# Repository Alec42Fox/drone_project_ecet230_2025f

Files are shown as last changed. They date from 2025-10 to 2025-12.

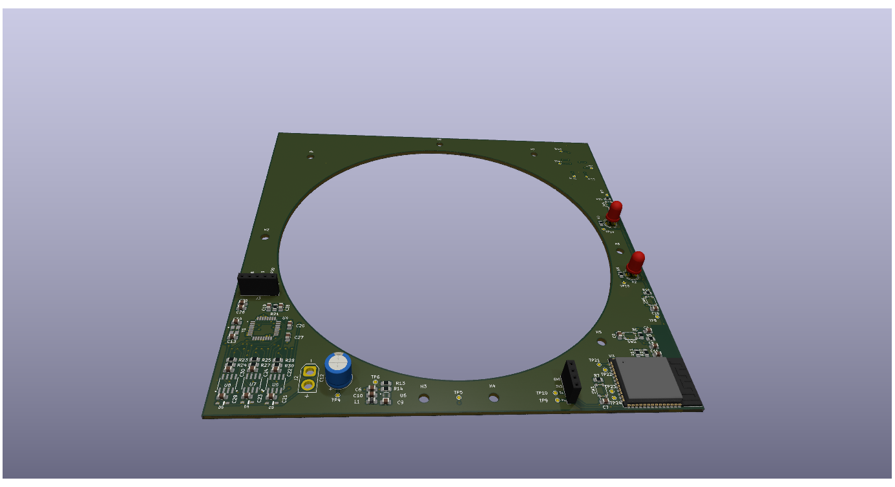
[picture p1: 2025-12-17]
Extra/HMS.png

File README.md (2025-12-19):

# ECET - 230 - 001 - HMS (Height Maintenance System)
* video of the prototype in action (fixed to a single axis)
* Also hyperlink to simulation below:
Watch the video (https://youtu.be/sBg5eHK91Yk)

View Our Project on CodePen (https://codepen.io/codaryu/pen/zxqgJxX)

## Goals
* Make a single propelled drone that hovers at a specific height and can get back to that height when outside forces act on it.
## Team Members
* Alec Fox - Programming
* Angelo McNeill - CAD Design
* Cristian D. Garcia S. - PCB Design
## Tools and Technologies
* Fusion 360 - 3D Design
* KiCad - PCB Design
* GitHub - Collaboration and Communication
## Timeline
| Phase | Duration | Description |
| :---: | :---: | :---: |
| Research Technology | Week 1 | Get the necessary electronics for the project with breakout boards and datasheets for future PCB design |
| CAD Design and Programming | Week 2 - 3 | Work on the design of the frame and chassis of the drone while working of the programming of the electronics |
| Proof of Concept | Week 4 - 5 | Use breakout boards and code to do testing and debugging |
| Looks-Like Prototype and Further Programming | Week 6 - 7 | Print the frame and chassis and do test to make sure they work well; also some programming on the side |
| PCB Design and Manufacturing | Week 8 - 9 | Make the PCB board that will have all the electronics and also buy it |
| Works-Like Prototype  | Week 10 | Test that the code works as intended |
| Engineering Prototype | Week 11 - 12 | Make the final prototype while testing and debugging; combining the looks-like and works-like prototypes|
## License
* The project uses an MIT license so our project is open-source. We do ask for attribution.

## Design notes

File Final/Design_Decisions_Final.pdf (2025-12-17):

# Design Decisions - Final

Microcontroller
- ESP32 S3 - A cheap yet powerful microcontroller that will be able to handle the job of powering the motor. It is lightweight too which makes it great for a project heavily based on weight.
Motor
- DYS SunFun 2306 - 1750KV Motor - Bigger than the POC propeller. Speeds up slower but can carry more weight and handle more current. Makes up to 1k grams of thrust which is overkill for the project. The propeller being used is still 5 inches in diameter. Motor Driver
- V-Good RC 32-Bit 30A 2-4S Brushless ESC - Works with the battery and the motor. The amount of max current is more than enough for the motor. Comes with SBEC but just needs the PWM and Ground pins to connect the ESP32 to the ESC.
Distance Sensor
- Adafruit VL53L0X - uses a laser to measure the distance. Has a range of up to 2 meters which is enough for this prototype. Just make sure the spot that the distance sensor uses to measure the distance is white for better reflectability.
Battery
- Lumenier 550mAh 4s 80c Lipo Battery - Has the required voltage for the motor and motor driver to run: both need 4s. The amount of current it can discharge is enough to cover the electronics.
Button (Switch)
- Button - used to turn the drone on/off. Could also look into adding more functions in the future. It’s easy to use and easy to implement to the hardware and software. Very lightweight.
Arduino IDE (Software)
- Used the Arduino IDE since it's simple to use and is compatible with the ESP32.

Current Block Diagram:

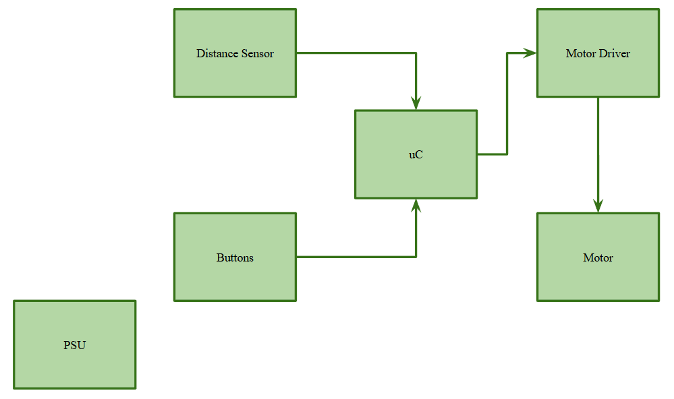
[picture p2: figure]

Current Bill of Materials:

Item | Link to Market Place | Status
Microcontroller | ESP32 S3 (https://www.amazon.com/dp/B0DG8L7MQ9?ref=ppx_yo2ov_dt_b_fed_asin_title&th=1) | Bought
Motor | SunFun (https://www.getfpv.com/dys-sunfun-2306-motor.html) | Bought
ESC | V-Good RC 32-Bit 30A 2-4S Brushless ESC (https://www.getfpv.com/v-good-rc-32-bit-30a-2-4s-brushless-esc-for-rc-airplane.html) | Bought
Distance | Adafruit VL53L0X Time of Flight Distance Sensor (https://www.adafruit.com/product/3317) | Bought
PSU | Lumenier 550mAh 4s 80c Lipo Battery (XT-30) (https://www.getfpv.com/batteries/mini-quad-batteries/lumenier-550mah-4s-80c-lipo-battery-xt-30.html) | Bought
Charger | Gens Ace iMars Mini G-Tech 60W 2-4S 5A (https://www.getfpv.com/batteries/battery-chargers/gens-ace-imars-mini-g-tech-60w-2-4s-5a-rc-eco-friendly-battery-charger-xt60.html) | Bought
Propeller | Gemfan Hurricane (https://www.getfpv.com/gemfan-hurricane-durable-51433-3-blade-propeller-set-of-4.html) | Bought
Button | N/A | Bought

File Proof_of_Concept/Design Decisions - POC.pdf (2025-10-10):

## Design Decisions - POC

### Microcontroller

- ESP32 S3 - A cheap yet powerful microcontroller that will be able to handle the job of powering the motor. It is lightweight too which makes it great for a project heavily based on weight.

### Motor

- BrotherHobby VY 1504.5 2650KV Motor - Makes thrusts in the 500 lbs which is more than enough for the project. This is enough thrust to have some headspace in case the weight of the chassis is more than was expected (combined with the weight of the electronics themselves and maybe friction). The propeller has to be 5 inches in diameter. Weight is also pretty low which is a plus.

### Motor Driver

- V-Good RC 32-Bit 30A 2-4S Brushless ESC - Works with the battery and the motor. The amount of max current is more than enough for the motor. Comes with SBEC but just needs the PWM and Ground pins to connect the ESP32 to the ESC.

### Distance Sensor

- Adafruit VL53L0X - uses a laser to measure the distance. Has a range of up to 2 meters which is enough for this prototype. Just make sure the spot that the distance sensor uses to measure the distance is white for better reflectability.

### Battery

- Lumenier 550mAh 4s 80c Lipo Battery - Has the required voltage for the motor and motor driver to run: both need 4s. The amount of current it can discharge is enough to cover the electronics.

### LED

- LED - have multiple LEDs as user interface showing the distance of the drone. For every 200 mm, an LED will turn on. The current max will be 5 LEDs at 1000 mm.

### Button (Switch)

- Button - used to turn the drone on/off. Could also look into adding more functions in the future. It’s easy to use and easy to implement to the hardware and software. Very lightweight.

### Current Block Diagram:

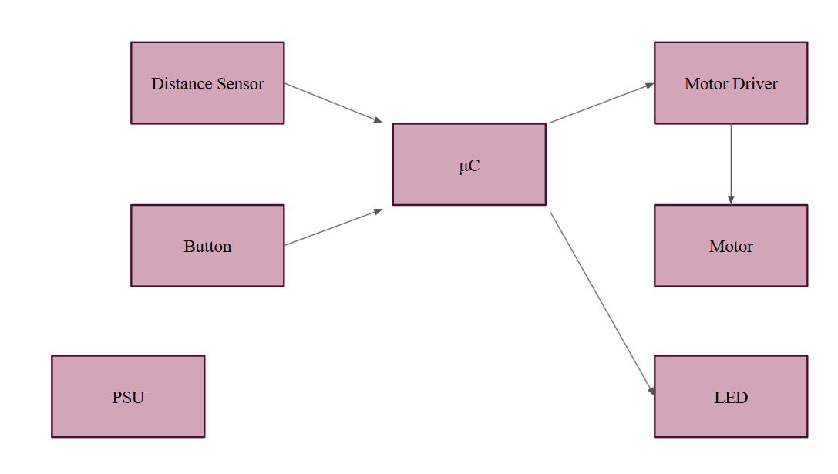
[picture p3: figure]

### Current Bill of Materials:

Item | Link to Market Place | Status
Microcontroller | ESP32 S3 (https://www.amazon.com/dp/B0DG8L7MQ9?ref=ppx_yo2ov_dt_b_fed_asin_title&th=1) | Bought
Motor | BrotherHobby VY 1504.5 2650KV (https://www.getfpv.com/brotherhobby-vy-1504-5-2650kv-2950kv-3950kv-motor.html) | Bought
ESC | V-Good RC 32-Bit 30A 2-4S Brushless ESC (https://www.getfpv.com/v-good-rc-32-bit-30a-2-4s-brushless-esc-for-rc-airplane.html) | Bought
Distance | Adafruit VL53L0X Time of Flight Distance Sensor (https://www.adafruit.com/product/3317) | Bought
PSU | Lumenier 550mAh 4s 80c Lipo Battery (XT-30) (https://www.getfpv.com/batteries/mini-quad-batteries/lumenier-550mah-4s-80c-lipo-battery-xt-30.html) | Bought
Charger | Gens Ace iMars Mini G-Tech 60W 2-4S 5A (https://www.getfpv.com/batteries/battery-chargers/gens-ace-imars-mini-g-tech-60w-2-4s-5a-rc-eco-friendly-battery-charger-xt60.html) | Bought
Propeller | Gemfan Hurricane SL 5125 3-Blade Propeller (https://www.getfpv.com/gemfan-hurricane-sl-5125-3-blade-propeller-1-5mm-shaft-set-of-4.html?vid=10995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) | Bought
LED | N/A | Bought
Button | N/A | Bought

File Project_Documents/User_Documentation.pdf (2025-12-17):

## User Documentation

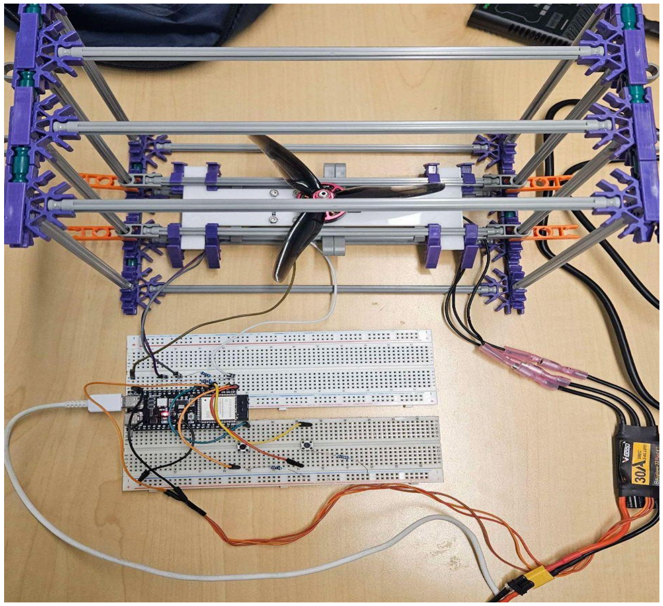
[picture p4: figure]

- The battery connects to the ESC.
- The ESC connects to the motor, where the wire connections matter to make sure the motor rotates the correct way.
- The ESC has a SBEC, which has three pins. The ones used for the project are the brown and orange. The brown connects to the ground of the ESP32 and the orange is connected to the 7 pin of the ESP32.
- The distance sensor has four pins that are being used. The white wire is connected to the 3V3 pin from the ESP32. The brown wire is ground. The purple wire was pin 9 and the grey wire was pin 8.
- The green and yellow wires are the input pins if the buttons are pressed. The green is pin 6 for hovering and the yellow is pin 15 for landing.
- The orange and red wires are 3V3 connected to the buttons.

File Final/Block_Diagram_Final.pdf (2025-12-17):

PSU

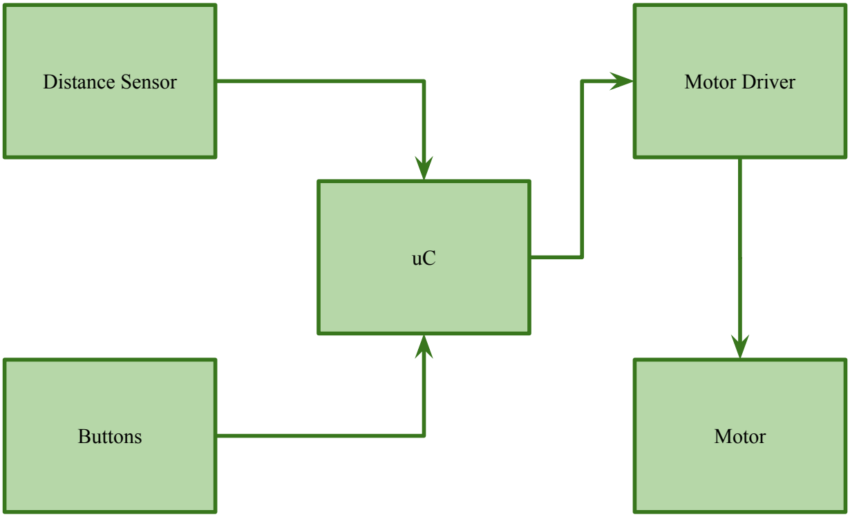
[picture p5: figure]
Buttons; Distance Sensor; Motor Driver; Motor

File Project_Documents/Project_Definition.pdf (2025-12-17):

## Project Definition

### TABLE OF CONTENTS

HIGH LEVEL DESCRIPTION | 1
PURPOSE | 1
COMMUNICATION | 1
OBJECTIVES | 1
SCENARIO | 1
USER INTERACTION STORIES | 1
USER INTERFACE | 2
USER ACCEPTANCE | 2
PARAMETERS | 3
TECHNICAL | 3
FUNCTIONS | 3
OPERATIONAL | 3
ENVIRONMENT | 3
FUTURE | 3
GLOSSARY | 3

### HIGH LEVEL DESCRIPTION

- AirLift or HMS (Height Maintenance System)
- Keeps itself at a desired height using a propeller. When it is pushed downward, pulled upward, has weight added to it, or has weight removed to it, it will change its speed to get back to the original desired height.

### PURPOSE

- The AirLift is a small piece to understanding the complexities that are required to build a drone. One of the biggest issues with making a drone is keeping the drone stable in the air while also moving. We are limiting the scope of the drone to simply stay hovering and be able to go up and down on one axis depending on outside forces. With the outside forces, it will know how to respond in order to get back to the same height it was hovering at originally.

### COMMUNICATION

- Github Repository (https://github.com/Alec42Fox/drone_project_ecet230_2025f)

### OBJECTIVES

- The AirLift is meant to be a single propeller drone that is autonomous and hovers at a specific height. I can get back to the original height even when weight is added or removed.

### SCENARIO

User Interaction Stories
- To begin using the drone, it has to be placed in the frame. Once in the frame and flat on the surface, it can be turned on using the button on the side.
- While running, the drone will simply hover. At this point, weight can be added in the designated areas to cause it to lower and it will then increase the thrust produced to get back to the original hovering position. It will do the opposite when weight is removed.
- To turn it off, make sure it's back to the original hover position and then press the button on the side.
- Red and Green LEDs are used as the user interface. Green means that the drone can be interacted with while red means to wait.
User Interface
- The user interface is based on red and green LEDs to show different states of the drone. The button on the side of the drone is used to turn it on or off.
User Acceptance
- Given-When-Then Criteria
- Given: Some external force
- When: The external force causes a change in height of the propeller
- Then: Propeller will change its motor speed to get back to the "equilibrium" point

- If the propeller always ends up at the same “equilibrium” point, it means that the purpose is being accomplished.

### PARAMETERS

Technical
- The design of the frame is still being worked on but it will be tall and will house the drone inside, limiting its movement to just up and down.
- The weight isn’t known yet but what is known is that it has to weigh around half of the thrust created by the propeller.
- The drone itself will have all the electronics in its chassis. The frame is separate from the frame.
Functions
- The drone can hover on its own at a distance dictated in the programming
- The drone can increase the thrust created to go up.
- The drone can decrease the thrust created to go down.
Operational
- The battery has to be big enough to power all the electronics but also last around a couple of hours for testing and demonstration.
Environmental
- The only thing is to have enough light so the laser of the distance sensor can work properly.

### FUTURE

- Use this knowledge to go for an actual drone with no frame to keep it moving only on one axis.

### GLOSSARY

- Drone - A device with a single motor that allows it to hover up and down.
- Chassis - The 3D printed housing of the drone. All electronics will be inside.
- Equilibrium Point - The starting height that the propeller will stay at and will always try to get to when outside forces are put onto it.

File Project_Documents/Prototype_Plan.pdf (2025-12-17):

## Prototype Plan

### Purpose

- We are going to outline the timeline of what we expect to do in each prototype we end up making for the Airlift/ HMS project

### Proof of Concept Prototype

- Alpha
Goals
- Show that the motor changes speed depending on the distance that is received by the microcontroller.
Type
- This is a proof of concept prototype
Scope
- The electronics included will be the microcontroller, motor, ESC, battery, and distance sensor
Timeline
- By October 21, 2025

### Looks-Like Prototype

- Beta
Goals
- Show how the chassis for the drone and the frame would most likely end up looking like Type
- This is a looks-like prototype
Scope
- Mainly 3-D printed design Timeline
- Sometime in mid November

### Works-Like Prototype

- Charlie
Goals
- Show that the motor works correctly with the distance that is being read. The hovering speed should happen at a specific distance and then should increase or decrease depending on the distance change. This would be done on a makeshift frame, not in the actual chassis or frame.
Type
- This is a works-like prototype
Scope
- The electronics included will be the microcontroller, motor, ESC, battery, distance sensor, and button
Timeline

- Sometime in the end of November to beginnings of December

### Engineering Prototype

- Delta
Goals
- Show that the chassis can hold all the electronics and that the drone can hover and get back to hovering at the original distance. The chassis and frame work well with each other. The software has little issues.
Type
- This is an engineering prototype
Scope
- The electronics included will be the microcontroller, motor, ESC, battery, distance sensor, LEDs, button, chassis of the drone, and frame of the drone
Timeline
- Mid to end of December

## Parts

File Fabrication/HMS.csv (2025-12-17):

Reference | Qty | Value | DNP | Exclude from BOM | Exclude from Board | Footprint | Datasheet | MFR | MPN
C1,C5,C7,C8,C9,C15,C17,C18,C19,C20,C25,C26,C27 | 13 | 0.1 uF |  |  |  | LibraryHMS_FSymbols_Library:C_0805_2012Metric_Pad1.18x1.45mm_HandSolder | ~ | KEMET | C0805C104K4RACTU
C2,C3,C6,C21,C23,C29 | 6 | 10 uF |  |  |  | LibraryHMS_FSymbols_Library:C_0805_2012Metric_Pad1.18x1.45mm_HandSolder | ~ | Samsung Electro-Mechanics | CL21A106KOQNNNE
C4 | 1 | 1 uF |  |  |  | LibraryHMS_FSymbols_Library:C_0805_2012Metric_Pad1.18x1.45mm_HandSolder | ~ | KEMET | C0805C105K4RACTU
C10 | 1 | 22 uF |  |  |  | LibraryHMS_FSymbols_Library:C_0805_2012Metric_Pad1.18x1.45mm_HandSolder | ~ | Samsung Electro-Mechanics | CL21A226MOQNNNE
C11,C16,C28 | 3 | 4.7 uF |  |  |  | LibraryHMS_FSymbols_Library:C_0805_2012Metric_Pad1.18x1.45mm_HandSolder | ~ | Samsung Electro-Mechanics | CL21B475KOFNFNE
C12 | 1 | 1000 uF |  |  |  | Capacitor_THT:CP_Radial_D8.0mm_P3.50mm | ~ | Nichicon | UVR1E102MPD
C13,C14 | 2 | 18 pF |  |  |  | LibraryHMS_FSymbols_Library:C_0805_2012Metric_Pad1.18x1.45mm_HandSolder | ~ | KEMET | C0805C180G4HACTU
C22,C24,C30 | 3 | 2.2 uF |  |  |  | LibraryHMS_FSymbols_Library:C_0805_2012Metric_Pad1.18x1.45mm_HandSolder | ~ | Murata Electronics | GRM21BR71C225KA12L
D1 | 1 | RED |  |  |  | LibraryHMS_FSymbols_Library:LED_D5.0mm | ~ | N/A | N/A
D2 | 1 | GREEN |  |  |  | LibraryHMS_FSymbols_Library:LED_D5.0mm | ~ | N/A | N/A
D3,D4,D5 | 3 | 1N4148WS |  |  |  | LibraryHMS_FSymbols_Library:SODFL2512X100N | https://www.vishay.com/docs/85751/1n4148ws.pdf
H1,H2,H3,H4,H5,H6,H7,H8 | 8 | MountingHole |  | Excluded from BOM |  | MountingHole:MountingHole_3.2mm_M3 | ~
J2 | 1 | 15V Input |  |  |  | LibraryHMS_FSymbols_Library:AMASS_XT30U-F_1x02_P5.0mm_Vertical | ~ | N/A | N/A
J3 | 1 | Conn_01x05_Socket |  |  |  | LibraryHMS_FSymbols_Library:PinSocket_1x05_P2.54mm_Vertical | ~ | N/A | N/A
J4 | 1 | Conn_01x04_Socket |  |  |  | Connector_PinSocket_2.54mm:PinSocket_1x04_P2.54mm_Vertical | ~ | N/A | N/A
L1 | 1 | 3.3 uH |  |  |  | LibraryHMS_FSymbols_Library:L_0805_2012Metric_Pad1.15x1.40mm_HandSolder | ~ | TDK Corporation | MLZ2012N3R3LT000
Q1,Q2 | 2 | BSS138 |  |  |  | LibraryHMS_FSymbols_Library:SOT-23-3_1P4X3P040_ONS | https://www.onsemi.com/pub/Collateral/BSS138-D.PDF | onsemi | BSS138
Q3,Q4,Q5,Q6,Q7,Q8 | 6 | TPH1R403NL,L1Q |  |  |  | LibraryHMS_FSymbols_Library:TPH1R403NLL1Q | https://www.mouser.in/ProductDetail/Toshiba/TPH1R403NLL1Q?qs=HVbQlW5zcXWxPmEVdb2K1w%3D%3D | Toshiba Semiconductor and Storage | TPH1R403NL,L1Q
R1,R2,R3,R4,R5,R6,R7,R14,R15,R16,R21,R22,R26,R29 | 14 | 10 K |  |  |  | LibraryHMS_FSymbols_Library:R_0805_2012Metric_Pad1.20x1.40mm_HandSolder | ~ | Susumu | RR1220P-103-D
R8 | 1 | 62.5 |  |  |  | LibraryHMS_FSymbols_Library:R_0805_2012Metric_Pad1.20x1.40mm_HandSolder | ~ | Panasonic Electronic Components | ERA-6AEB101V
R9 | 1 | 60 |  |  |  | LibraryHMS_FSymbols_Library:R_0805_2012Metric_Pad1.20x1.40mm_HandSolder | ~ | Panasonic Electronic Components | ERA-6AEB101V
R10,R11 | 2 | 4.7 K |  |  |  | LibraryHMS_FSymbols_Library:R_0805_2012Metric_Pad1.20x1.40mm_HandSolder | ~ | Vishay Dale | CRCW08054K70FKEAC
R12,R17,R18,R19,R31,R32 | 6 | 100 |  |  |  | LibraryHMS_FSymbols_Library:R_0805_2012Metric_Pad1.20x1.40mm_HandSolder | ~ | Panasonic Electronic Components | ERA-6AEB101V
R13 | 1 | 31.6 K |  |  |  | LibraryHMS_FSymbols_Library:R_0805_2012Metric_Pad1.20x1.40mm_HandSolder | ~ | Panasonic Electronic Components | ERA-6AEB3162V
R23,R24,R25,R27,R28,R30 | 6 | 33 K |  |  |  | LibraryHMS_FSymbols_Library:R_0805_2012Metric_Pad1.20x1.40mm_HandSolder | ~ | YAGEO | RC0805FR-0733KL
SW1,SW2,SW5,SW6 | 4 | PTS810_SJM_250_SMTR_LFS |  |  |  | LibraryHMS_FSymbols_Library:SW_PTS810_SJM_250_SMTR_LFS |  | C&K | PTS810SJS250SMTR LFS
TP1,TP2,TP3 | 3 | TestPoint_Small |  |  |  | TestPoint:TestPoint_Pad_1.0x1.0mm | ~ | N/A | N/A
TP4,TP5,TP6,TP7,TP8,TP9,TP10,TP11,TP12,TP13,TP14,TP15,TP16,TP17,TP18,TP19,TP20,TP21,TP22,TP23,TP24 | 21 | TestPoint_Small |  |  |  | LibraryHMS_FSymbols_Library:TestPoint_Pad_D1.0mm | ~
U1 | 1 | VL53L0CXV0DH/1 |  |  |  | LibraryHMS_FSymbols_Library:LGA12_STM | https://www.st.com/resource/en/datasheet/vl53l0x.pdf | STMicroelectronics | VL53L0CXV0DH/1
U2 | 1 | MIC5255-2.8YM5-TR |  |  |  | LibraryHMS_FSymbols_Library:SOT-23-5_M5_MCH | MIC5255-2.8YM5-TR | Microchip Technology | MIC5255-2.8YM5-TR
U3 | 1 | ESP32-S3-WROOM-1 |  |  |  | LibraryHMS_FSymbols_Library:ESP32-S3-WROOM-1 | https://www.espressif.com/sites/default/files/documentation/esp32-s3-wroom-1_wroom-1u_datasheet_en.pdf | Espressif Systems | ESP32-S3-WROOM-1-N4
U4 | 1 | ATMEGA328P-AU |  |  |  | LibraryHMS_FSymbols_Library:QFP80P900X900X120-32N |  | Microchip Technology | ATMEGA328P-AU
U5,U7,U8 | 3 | IR2101STRPBF |  |  |  | LibraryHMS_FSymbols_Library:SO8N_INF | https://www.infineon.com/dgdl/ir2101.pdf?fileId=5546d462533600a4015355c7a755166c | Infineon Technologies | IR2101STRPBF
U6 | 1 | AP62150Z6-7 |  |  |  | LibraryHMS_FSymbols_Library:SOT563_DIO | AP62150Z6-7 | Diodes Incorporated | AP62150Z6-7
Y1 | 1 | ABM8G-16.000MHZ-18-D2Y-T |  |  |  | LibraryHMS_FSymbols_Library:XTAL_ABM8G-16.000MHZ-18-D2Y-T |  | Abracon LLC | ABM8G-16.000MHZ-18-D2Y-T

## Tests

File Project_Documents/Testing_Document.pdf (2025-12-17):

## Testing Document

- Build the the frame and chassis out of knex
- Have space to place the plate which will hold the motor and distance sensor
- Make the proper connections between the ESP32, ESC, distance sensor, and buttons.
- The connections are as follows:
■ Buttons are connected to pin 6 and 15. 6 is for hover and 15 is for land.
■ Distance sensor is connected on pins 8 and 9. 8 is for SDA and 9 is for SCL.
■ The rest of the connections are to give proper voltage and grounding everything to the same point.
- When everything is connected, first make sure the motor and distance sensor sets up right before pressing the hovering button.
- When the hovering button is pressed, the motor will get to the distance put in the code. At this point, it will hover and can be moved to see the motor get back to the desired position.
- When wanting to land the motor, the button can be pressed. Allow the motor to lower on its own and make sure it turns off before touching the motor.
- The current setup allows for connection where the ESP32 connects to a computer and information can be seen through the serial monitor. The other is powering everything through the battery but won’t get access to the serial monitor.

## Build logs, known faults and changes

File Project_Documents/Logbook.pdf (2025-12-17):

## Logbook

09/09/2025
- The original idea was to make a drone, but it is way too complicated for one semester.
- Our project can be described as a dumbwaiter that uses a propeller instead of mechanical parts.
- We are using a single motor to power a propeller that goes up to a point considered "equilibrium”. Weight, push, or pull forces can be done on the propeller. That would lead to the propeller increasing or decreasing speed to get back to the "equilibrium” point.
- The electronics we so far need are as follows: switches (x2), psu (x1), distance sensor (x1), brushless DC motor (x1), motor driver (x1), and microcontroller (x1).
- Distance sensor we might use (https://www.google.com/search?q=VL53L0X&rlz=1C1VIQF_enUS1100US1100&sourceid=chrome&ie=UTF-8)
- Have to talk about it but might add a display
- A frame of sorts is going to be needed to keep the propeller stationary in the x and y direction, only moving in the z direction.
- Current block diagram:

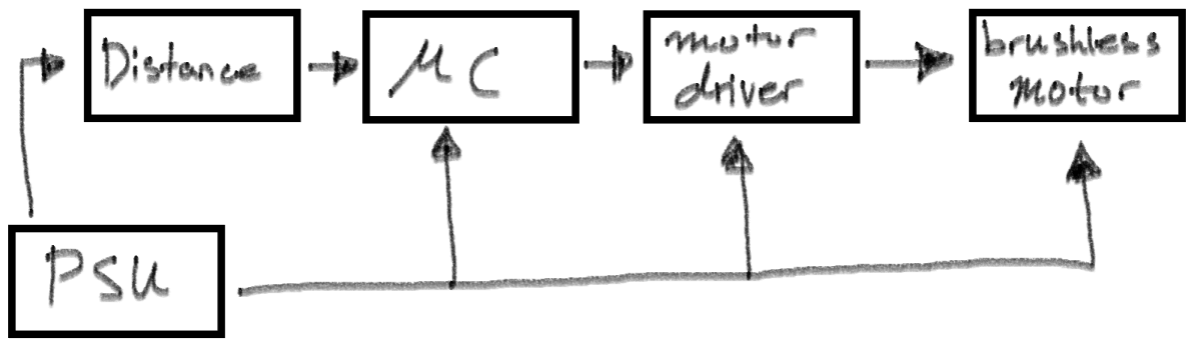
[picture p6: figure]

- Possible design:

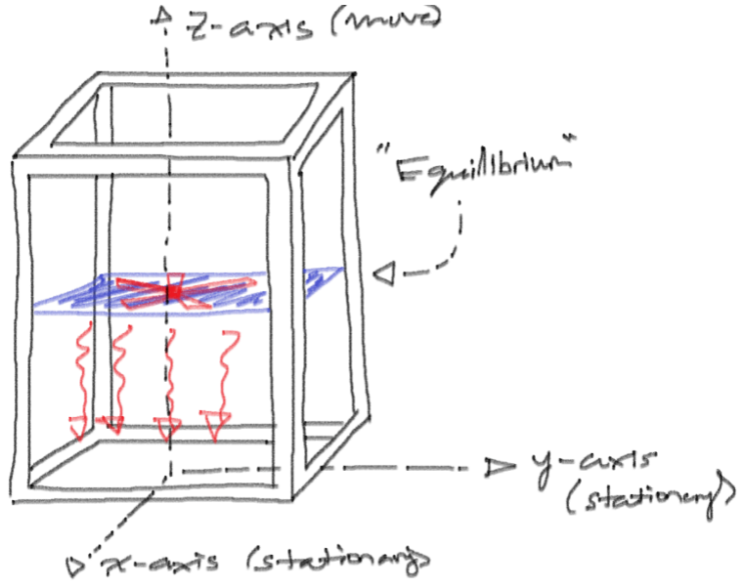
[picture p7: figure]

09/11/2025
- There is another possible design for the frame that uses like 3 to 4 poles and that is what keeps the drone travelling only on the z-axis.
- We have decided that the drone will have all of its electrical components in one place which means the frame is just a structure to hold it in place.
- The button to turn the drone on and off will be on one side which keeps us away from using wires to connect all the electronics together.
- The electronics will probably mostly be placed in the center or in a way that the weight is evenly distributed.
- The motor and propeller we use will have to create enough downward force to move the drone up and down.
- The electronics we so far need are as follows: switches (x1), psu (x1), distance sensor (x1), brushless DC motor (x1), motor driver (x1), and microcontroller (x1). We also have to look into a voltage regulator since the drone would be running on a battery for power.
- Updated block diagram from last time:

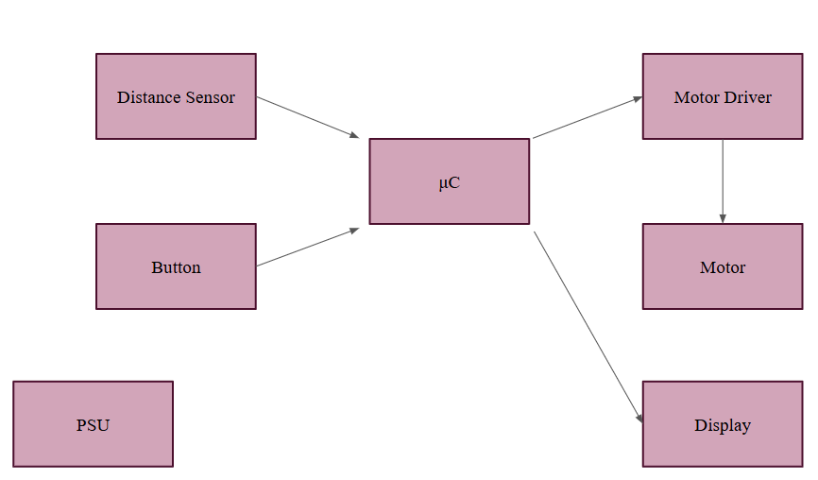
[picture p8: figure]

09/14/2025
- New block diagram:

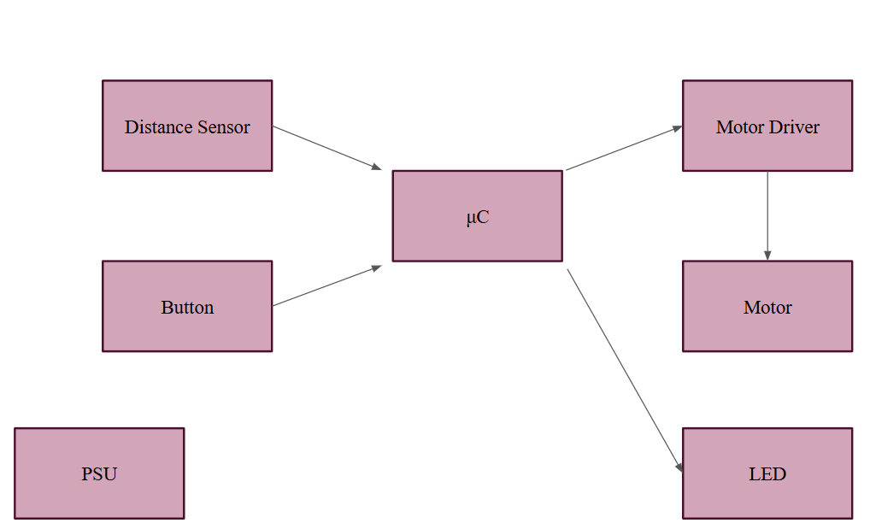
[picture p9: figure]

- Originally, we were thinking of using a display for giving user feedback about the drone but an LED was decided to be easier for this current prototype.
- The electronics we so far need are as follows: switches (x1), psu (x1), distance sensor (x1), brushless DC motor (x1), motor driver (x1), LED (x1), and microcontroller (x1). We also have to look into a voltage regulator since the drone would be running on a battery for power.
- Links to some electronics:
- Microcontroller (https://www.espressif.com/en/products/socs/esp32) - Multiple ones we can choose from
- Distance Sensor (https://www.adafruit.com/product/3317) - The one professor talked about
- LED (https://www.digikey.com/en/products/detail/dialight/5218559F/12178444?gclsrc=aw.ds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) - Any RGB LED will do, just have it there for reference
- Button (https://www.digikey.com/en/products/detail/omron-electronics-inc-emc-div/B3U-1100PM/3908607?gclsrc=aw.ds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) - Just have this button for reference, what ever is best
- Looking into motors, specifically for drones, there are some things to be aware of. Most specify the number of cells the LiPo battery has using “xS”. So 4S is 4 cells in series. To find the thrust they can produce, we can just look at the manufacturer’s info.
- Possible motor with ESC (https://www.aliexpress.us/item/3256801499398198.html) - So the number of cells needed would be 4S and can max thrust 1024 g. From reading online, a good thrust-to-weight ratio is 2:1 for the basic movements of a drone which should be more than enough for us. The motor and ESC need like 4s which is almost 15 volts.
- A single LiPo cell is around 3.7 volts.
- Possible battery (https://genstattu.com/tattu-650mah-4s-15-2v-95c-lipo-battery-long-pack-with-xt30-plug/)
- Need a buck converter. If not, the battery will kill the ESP32.
- Possible names: AirLift or HMS (Height Maintenance System).

- Other possible design:

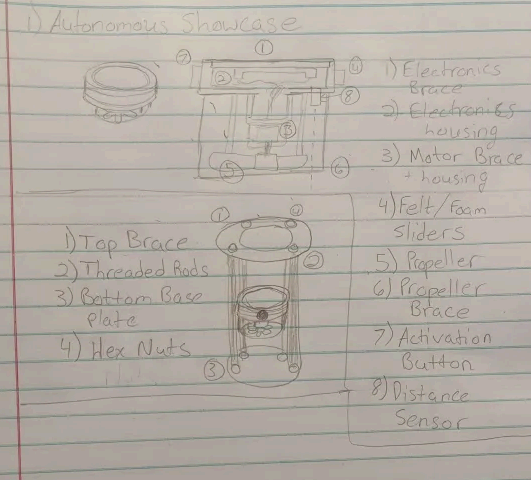
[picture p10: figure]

09/17/2025
- Concern arose about horizontal space dedicated to house the laser. Having the laser hang over the propeller would risk the distance data being skewed.
- By pushing the laser to the outer perimeter of the propeller’s range, we increase the overhang of the drone.
- Looked into the electronics we will use again and landed on this possible list:
- Distance -
https://www.adafruit.com/product/3317?srsltid=AfmBOophG-wvvBTgmJzAP-8j hGge4Poar271QmEji-KDwoUUaXPynfFA (https://www.adafruit.com/product/3317)
- Microcontroller -
https://www.digikey.com/en/products/detail/espressif-systems/ESP32-S3-DEVKITC-1U-N8R8/16162636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 (https://www.digikey.com/en/products/detail/espressif-systems/ESP32-S3-DEVKITC-1U-N8R8/16162636?gclsrc=aw.ds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)
- Motor -
https://www.getfpv.com/brotherhobby-vy-1504-5-2650kv-2950kv-3950kv-motor. html (https://www.getfpv.com/brotherhobby-vy-1504-5-2650kv-2950kv-3950kv-motor.html)
- ESC -
https://www.getfpv.com/v-good-rc-32-bit-30a-2-4s-brushless-esc-for-rc-airplane.html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 20799936859&network=x&device=c&gc_id=20799936859&gad_source=1&gad _campaignid=20796067361&gbraid=0AAAAAD8cN5LjXoJDnIXa5zmCuLtj7zx SZ&gclid=Cj0KCQjwuKnGBhD5ARIsAD19RsYVdS8y1Dh9E5zQdFk1-bCXJu klTw65ExcxBI9Z00ZKhiOYvTiip78aAuW0EALw_wcB (https://www.getfpv.com/v-good-rc-32-bit-30a-2-4s-brushless-esc-for-rc-airplane.html?afid=aVlOV0hBdmd6THc9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)
- Battery -
https://www.getfpv.com/batteries/mini-quad-batteries/lumenier-550mah-4s-80c-li po-battery-xt-30.html (https://www.getfpv.com/batteries/mini-quad-batteries/lumenier-550mah-4s-80c-lipo-battery-xt-30.html)
- LEDs and Buttons are just generic, don’t have to be anything special
- Decided on two LEDs: one red and one green. This will tell the user when they can actually interact with the drone.

09/18/2025
- Current Bill of Materials:
Electronic | Link to Market Place | Status | Cost
Microcontroller | ESP32 S3 (https://docs.espressif.com/projects/esp-matter/en/latest/esp32s3/index.html) | Bought
Motor | XING-E PRO 2207 2450KV (https://shop.iflight.com/xing-e-pro-2207-2-6s-fpv-nextgen-motor-pro874) | Available
ESC | | Available
Distance | Adafruit VL53L0X Time of Flight Distance Sensor (https://www.adafruit.com/product/3317) | Available
PSU | Lumenier 550mAh 4s 80c Lipo Battery (XT-30) (https://www.getfpv.com/batteries/mini-quad-batteries/lumenier-550mah-4s-80c-lipo-battery-xt-30.html) | Available
Charger | Gens Ace iMars Mini G-Tech 60W 2-4S 5A (https://www.getfpv.com/batteries/battery-chargers/gens-ace-imars-mini-g-tech-60w-2-4s-5a-rc-eco-friendly-battery-charger-xt60.html) | Available
Propeller | Gemfan Hurricane SL 5125 3-Blade Propeller (https://www.getfpv.com/gemfan-hurricane-sl-5125-3-blade-propeller-1-5mm-shaft-set-of-4.html?vid=10995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) | Available
LED | N/A | Bought
Button | N/A | Bought
Buck Regulator | N/A | Available
LDO | N/A | Available
3.5V Beeper | N/A | Available
TVS diode | N/A | Available
polyfuse at V in | N/A | Available
capacitors | N/A | Available
MOSFET | N/A | Available
- Trying to buy most electronics to be able to begin getting things to run.
- Added extra components for the safety of the main electronics.
- https://esp32.com/viewtopic.php?t=20450 Info on how to interface with the ESC Using the ESP32. It might be a bit of a hassle, but according to this it’s possible.

09/24/2025
- Updated the README in github
- Buying the components by today and making sure they have datasheets to go with the electronics.
- Division of work for the project: Alec - Programming, Angelo - CAD, Cristian - PCB

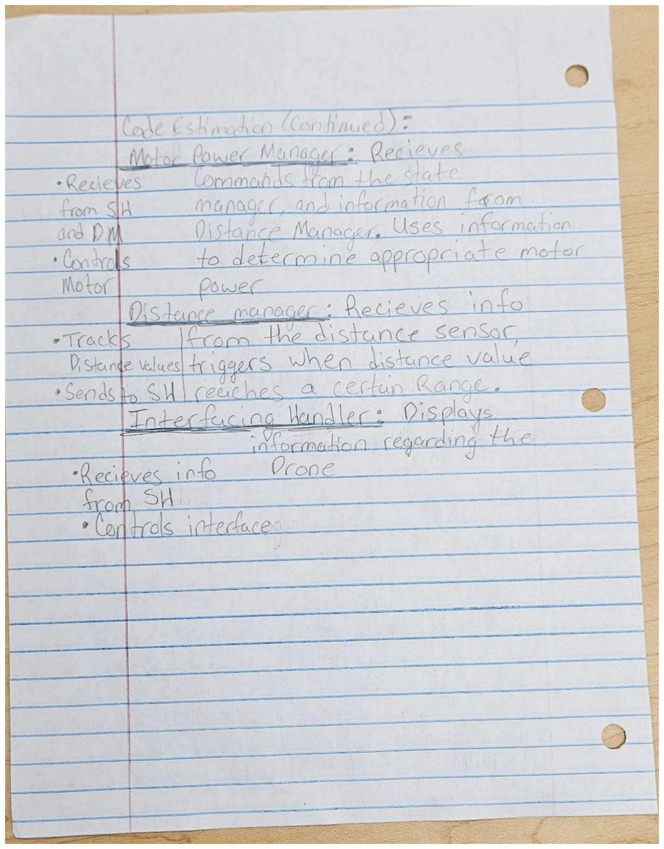
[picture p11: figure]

●

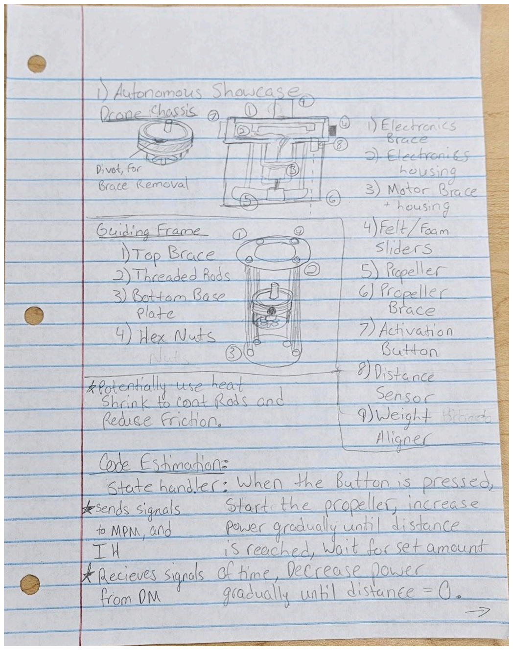
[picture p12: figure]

- https://www.instructables.com/Build-Custom-ESP32-Boards-From-Scratch-the-Complet/
- Maybe it would be good to have two buttons: one that turns the drone on/off and another that initiates hovering and the other to land. The latter would have three states. The first is standby, then hovering, and finally landing. After the landing, the button would go back to the standby state so the drone could be turned off. Just have to think of the code so the drone can turn on and off safely.

09/30/2025
- Have two 4.7 k ohm resistors parallel to SDL and SDA lines connected to the voltage value of the ESP32. They can stay open assuming they don’t end at some sensor.
- The GPIO pins for SDL and SDA for the ESP32 we are using are 21 and 22. 21 is SDA and 22 is SCL. The pins can be changed though.
- upesy.com/blogs/tutorials/esp32-pinout-reference-gpio-pins-ultimate-guide
- Have to check which GPIO pins are going to be used and which ones can be marked for no use.
- Waiting mostly on the ESC to be used to see if voltage regulators are needed or if the ESC has it itself.
- Distance Sensor Library (https://github.com/adafruit/Adafruit_VL53L0X)
- ESP32 Servo Library (https://docs.arduino.cc/libraries/esp32servo/)

10/01/2025
- Found some resources in order to make our own ESC for the actual prototype.
- We are going to have to use a ST-Link to program the STM chip with AM32. AM32 is the firmware used for STM chips which have a 32 bit ARM processor.
- https://www.youtube.com/watch?v=K9toWUsjgkE&list=PLoPtpxJIxgnbG5owAAyvgVvzenaRd1DPr&index=3 (https://www.youtube.com/watch?v=K9toWUsjgkE&list=PLoPtpxJIxgnbG5owAAyvgVvzenaRd1DPr&index=3)
- https://www.youtube.com/watch?v=sau_KQx4EIA&list=PLoPtpxJIxgnbG5owAAyvgVvzenaRd1DPr&index=3 (https://www.youtube.com/watch?v=sau_KQx4EIA&list=PLoPtpxJIxgnbG5owAAyvgVvzenaRd1DPr&index=3)
- https://www.youtube.com/watch?v=-ymTE-Nivzw&t=344s

10/06/2025
- For the ESC, I decided to go with a different design from another guy because he shows actual testing.
- Changed the BOM and Design Decisions to reflect the electronics needed for the Proof of Concept. The extra electronics are for the actual PCB design and can be omitted for now.
- Since sensitive parts need 3.3V, and battery can run out and drop below that, a warning system for this is needed, hence a beeper starting at around 3.5V
- planned part: 1-8S LiPo Low Voltage Buzzer Alarm
- Miscellaneous parts to foolproof it from getting fried from mistakes
- 22-100 μF electrolytic on input to MP1584 buck, plus 0.1-1 μF ceramic at X5R/X7R
- polyfuse at battery input to protect buck/ESC/etc. (to protect ESP from bursts of current)
- p-channel MOSFET, backwards to block reverse polarity, as diode with low drop (to not fry stuff if battery is connected incorrectly)
- TVS diode is needed because plugging/unplugging LiPo, or motor switching noise, might be an issue due to voltage spikes
- Buck Regulator MP1584, sensitive parts (esp32, sensors) need 3.3V or they get fried
- LDO (one of the following parts will suffice; LDO needed to clean up noise of buck reg)
- AMS1117 − 3.3
- AP7333

10/10/2025
- Changes to github adding design decisions and BOM documents for the POC. The POC code has also been added. The rough draft of the schematic is also added.
- The POC is mostly done and uses the items listed in the BOM.
- Got the motor to base its speed off the distance being read by the V53L0X. At the same time, there are 5 LEDs, with each one lighting up when the distance is increased by 200 mm. There is also a button used to turn on and off the motor and distance sensor without removing the power. Currently, the POC is connected to the USB port of my computer.
- After testing, the ESC is able to deliver enough power to make the POC run off the power of the battery and not be connected to a computer.
- Test that I did for the drone:
- Test a blinking LED code
- Test code for distance sensor
- Test a blinking LED with button
- Test distance sensor while turning LEDs on depending on the range of distance
- Get the motor speed to change with the number of LEDs that are turned on depending on the range of distance being read by the distance sensor
- Add a button to turn the device on or off
- Use the battery as a source for the ESP32 as well

10/21/2025
- Add ferrite beads before capacitors for noise reduction
- Put distance sensor in one of the corners away from the esc
- Shorten the distance between the esc, battery connector, and motor connector
- Could also try making the traces thicker, adding vias between two traces both carrying the battery voltage, also removing the mask on top of the traces so solder can be added to add wiggle room

10/23/2025
- We are looking into doing tests for the code but would need to make a custom chassis. We are looking into making one out of legos (or similar toys) for an early design and then making two 3D prints. At the same time, making these early designs would make it easier for us to make the final prototype down the line, already knowing designs that work.
- The PCB design has been worked on in the background but still needs to make changes to further improve how it would fit into the chassis that is still being worked on and making sure the voltage and current is proper for all the electrical components.
- The weight of all the main electronics used in the POC is about 120g. These are going to be used to put it inside the custom chassis so code testing can begin.
- This is information about the screws: (https://accu-components.com/us/metric-cap-head-screws/3957-SSCF-M2-14-A4?google_shopping=1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) 1.5 mm size for the holes x 4.

10/28/2025
- Change the schematic and PCB layout to correctly connect the crystal for the atmega chip
- Use two 18 pF capacitors parallel to each of the lines.
- ESC stopped working and now have to check if its soldering issues. Trying to fix it but also have a new one coming in case.
- To save space, the final design will only have pins (or sockets) to program the chips using FTDI. ESP32 has a sequence for the buttons in order to flash new information.
- For FTDI on the Atmega328p, five pins are going to be used and four for the ESP32.
- The Atmega328p can have a simple automatic circuitry for uploading new software to it but the ESP32 has to use the right combination of pressing the BOOT and RESET buttons.
- Need an external FTDI programmer and will use these pins: Rx, Fx, GRN, VCC, DTR. The last is only for the Atmega so manual buttons are not needed but are for ESP32
- Have the option of going with two MCUs, one for the ESC and another for talking between the sensors and ESC, or a single one that does everything
- Might have to switch to new ESC for testing the code

12/11/2025
- The hovering works but the distance sensor is currently not on the plate so it's us physically changing the height.
- Have to add the function to be able and land when another button is pressed.
- Have to make a new plate that holds the distance sensor on it as well and has longer wires.
- In the code, the PID values have to keep being changed to get satisfactory results.
- The frame made out of knex works good enough to show a presentation.
- The height of the frame is 210 mm, so we can aim for like 180 mm of hovering height.
- All the electronics will be outside of the frame with wires being used to connect everything.

12/17/2025
- The distance sensor and motor are on the same plate and the code works as intended.
- The frame sometimes gets stuck on the sides when trying to land but the hovering works as expected.
- Finishing the KiCAD and CAD models so they align with each other.

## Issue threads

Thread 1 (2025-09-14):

Research Electronics

CrisDavid9, 2025-09-14:
Finding what are the 7 electronic pieces we are going to buy for the project:
1. Motor
2. Motor Driver
3. PSU
4. Microcontroller
5. Distance Sensor
6. RGB LED
7. Button

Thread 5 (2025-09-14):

Combine distance sensor with motor and motor driver

CrisDavid9, 2025-09-14:
With the motor and driver working, we can test out the distance sensor and show that we get the proper outcomes

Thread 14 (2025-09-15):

PSU

CrisDavid9, 2025-09-15:
From a small amount of research, some of the competition drones use motors which require 15 V. Might have to end up going with such a battery and the correct electronics to step the voltage down when connecting the microcontroller and other components.

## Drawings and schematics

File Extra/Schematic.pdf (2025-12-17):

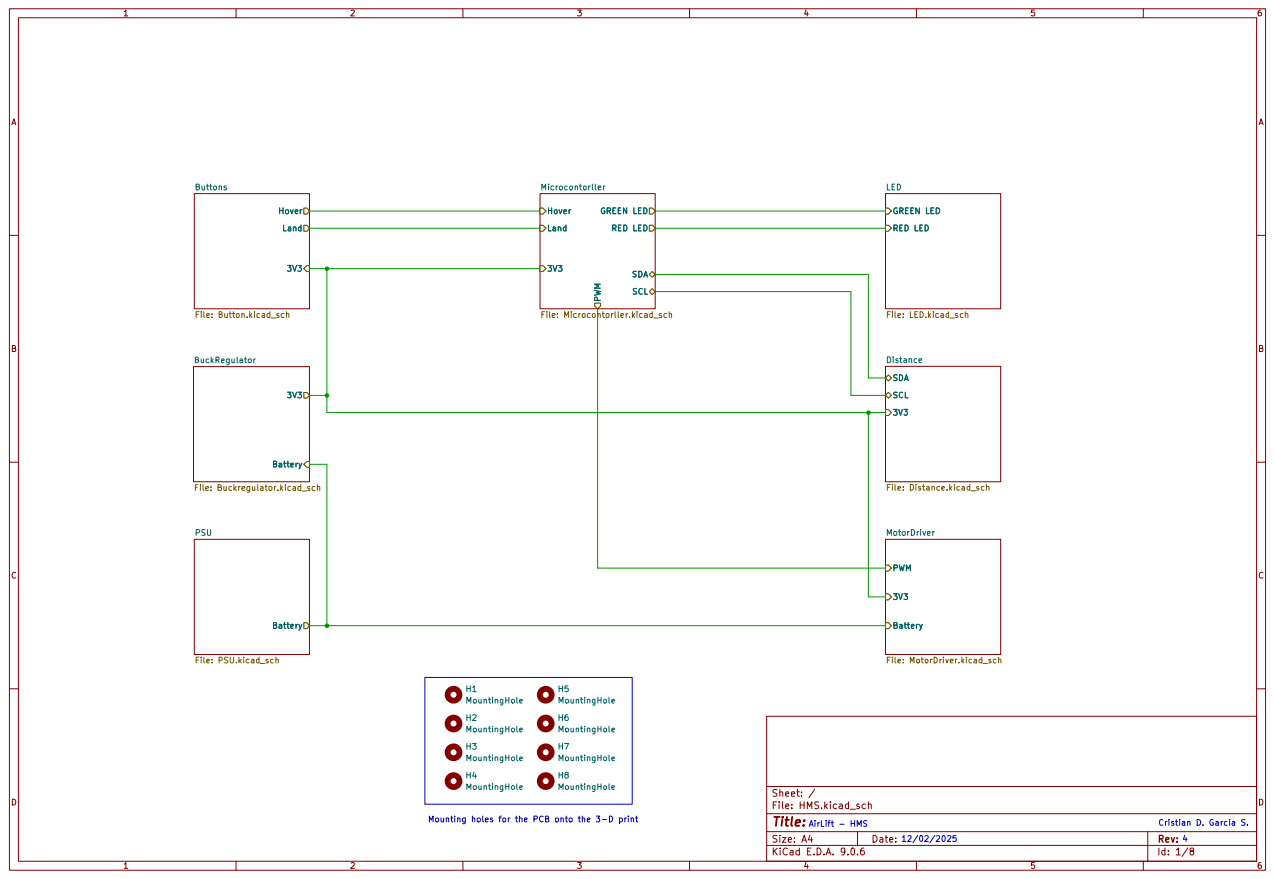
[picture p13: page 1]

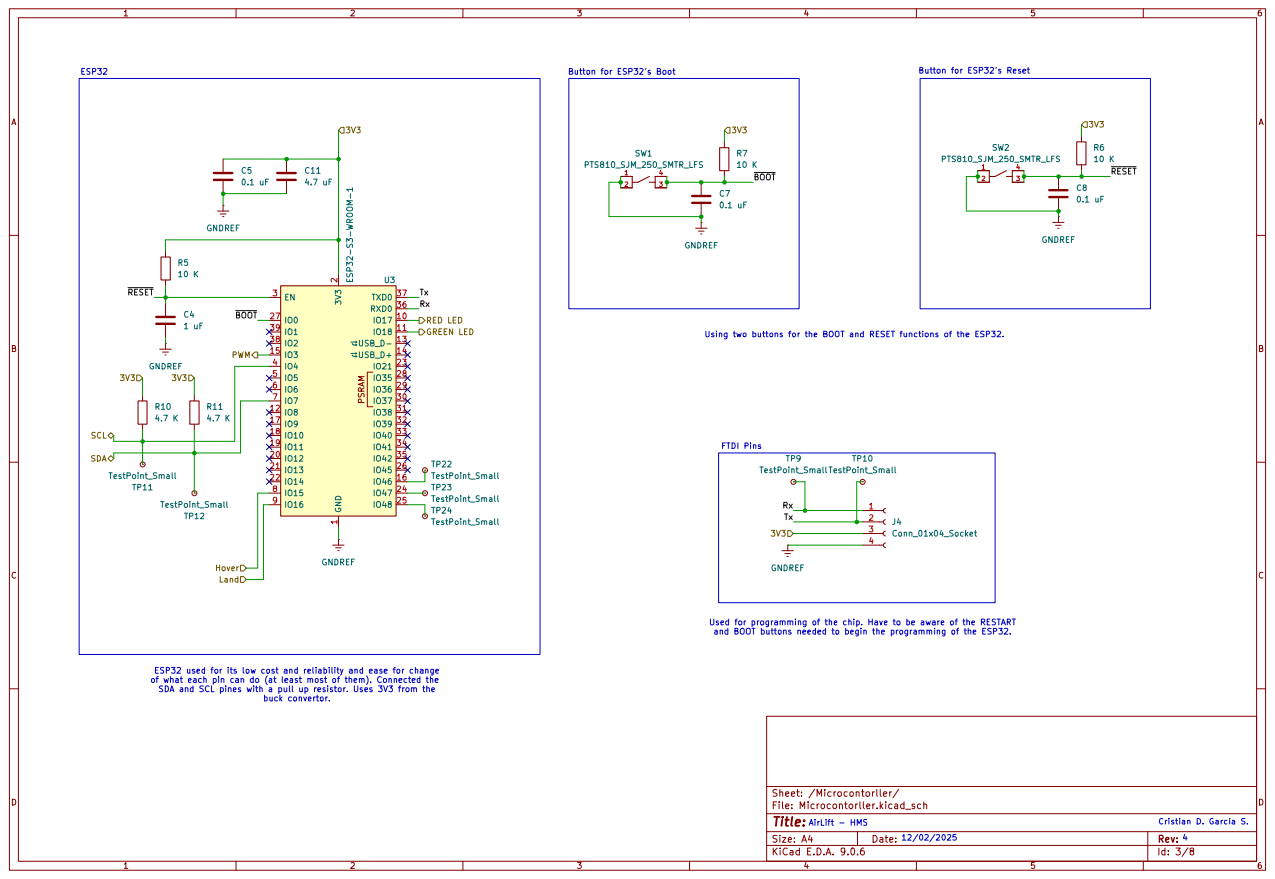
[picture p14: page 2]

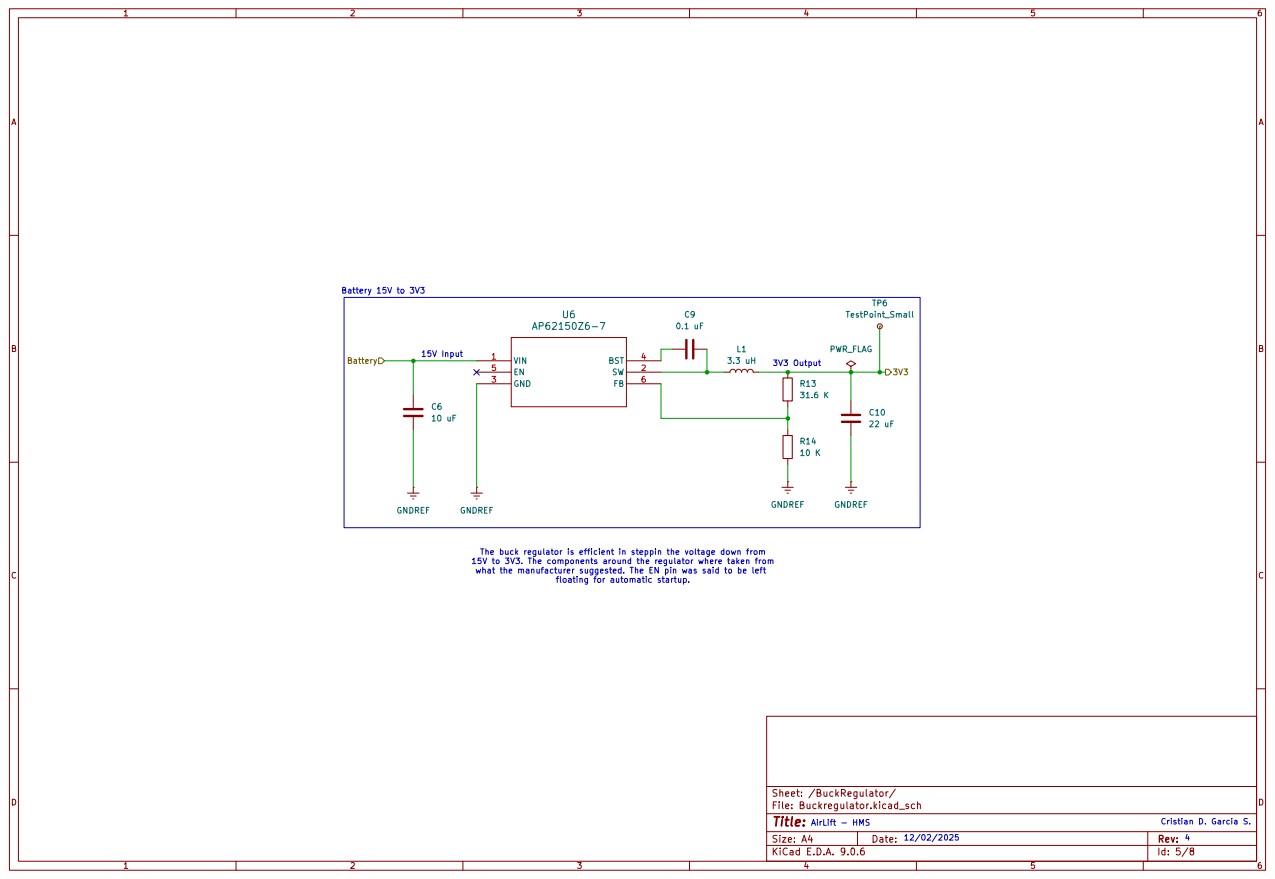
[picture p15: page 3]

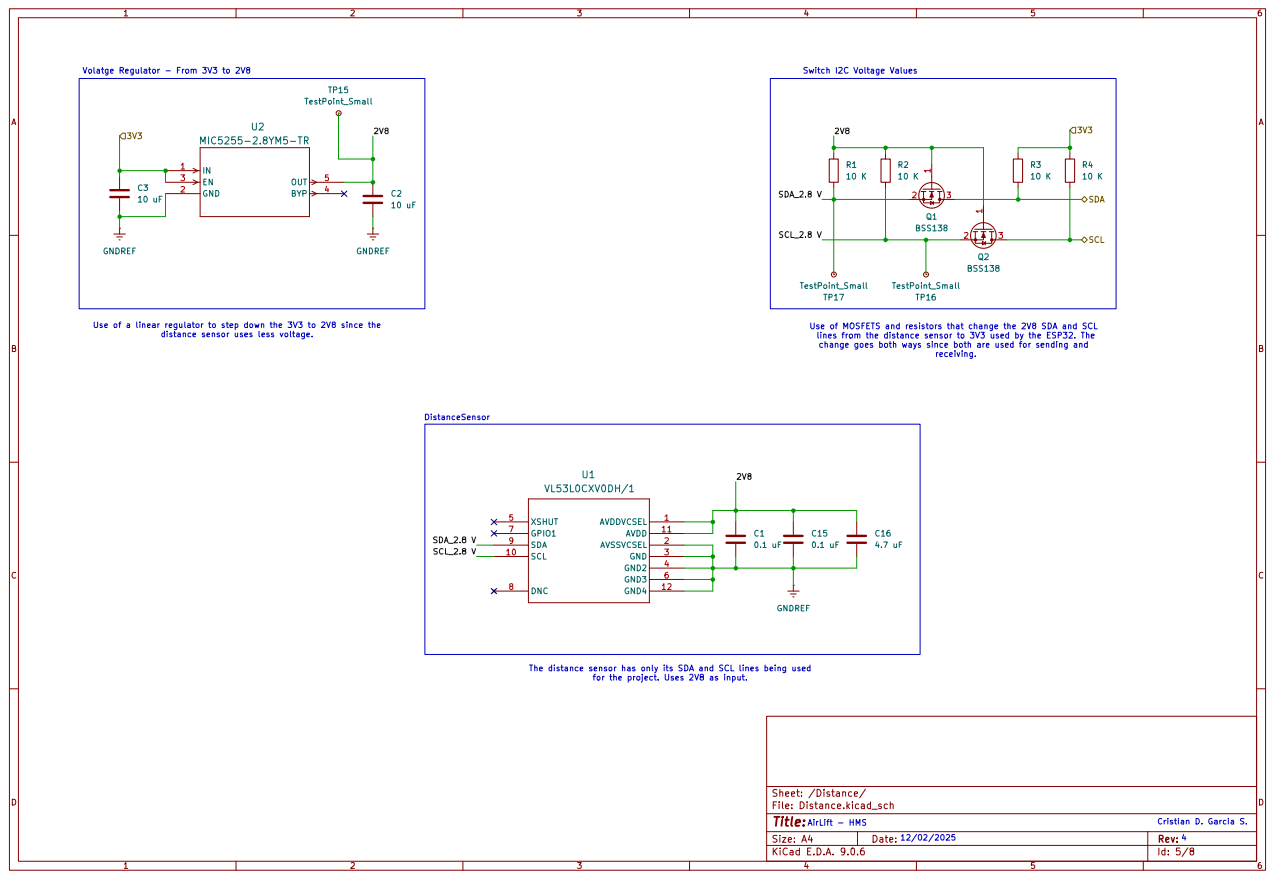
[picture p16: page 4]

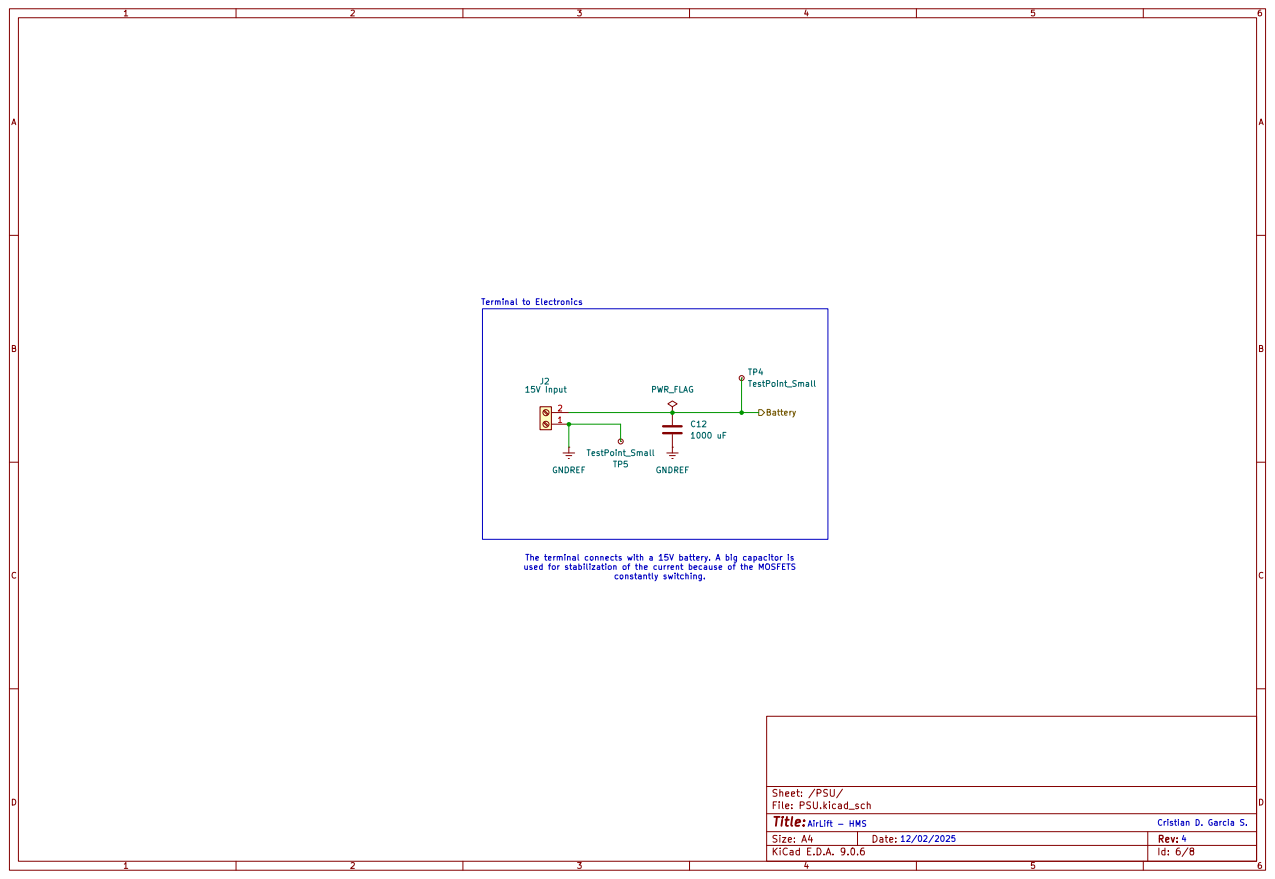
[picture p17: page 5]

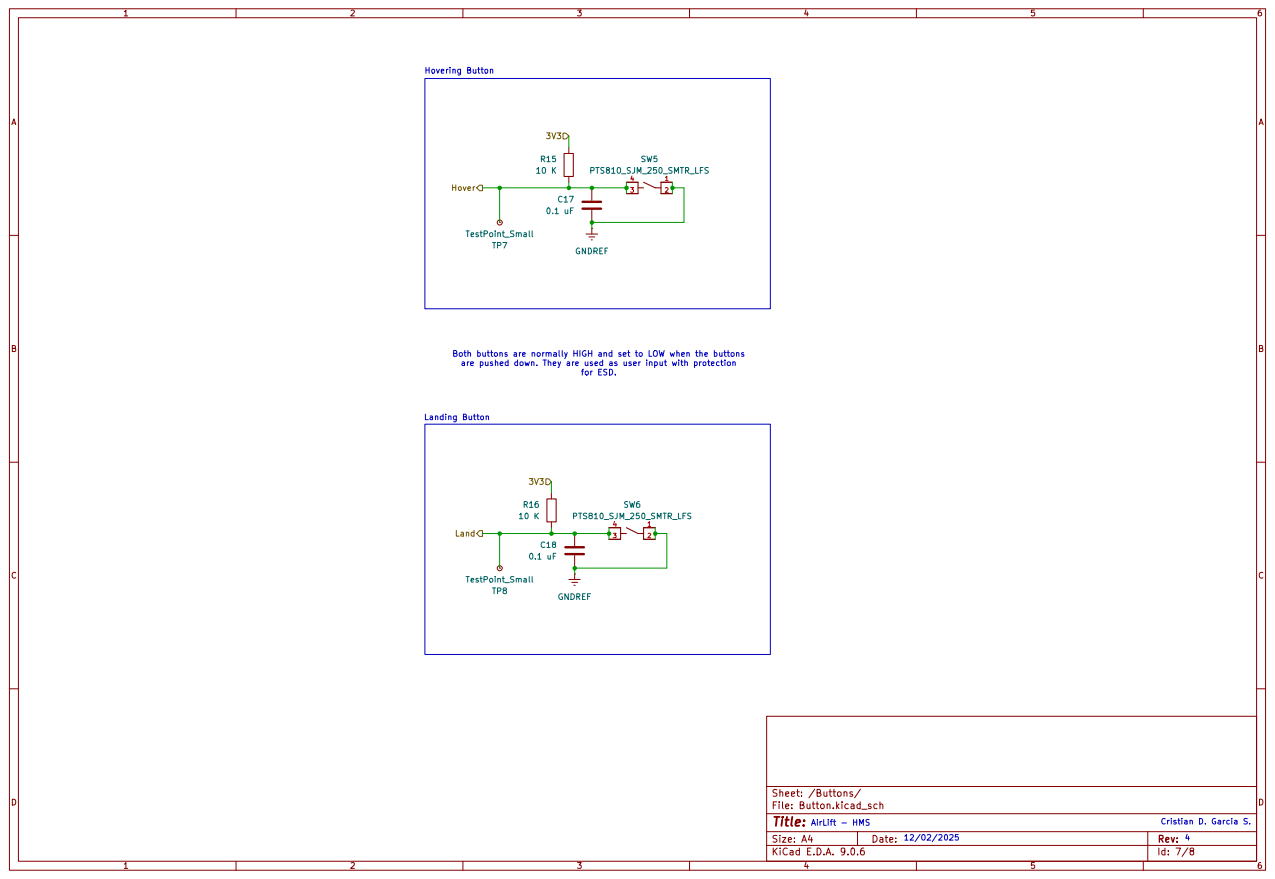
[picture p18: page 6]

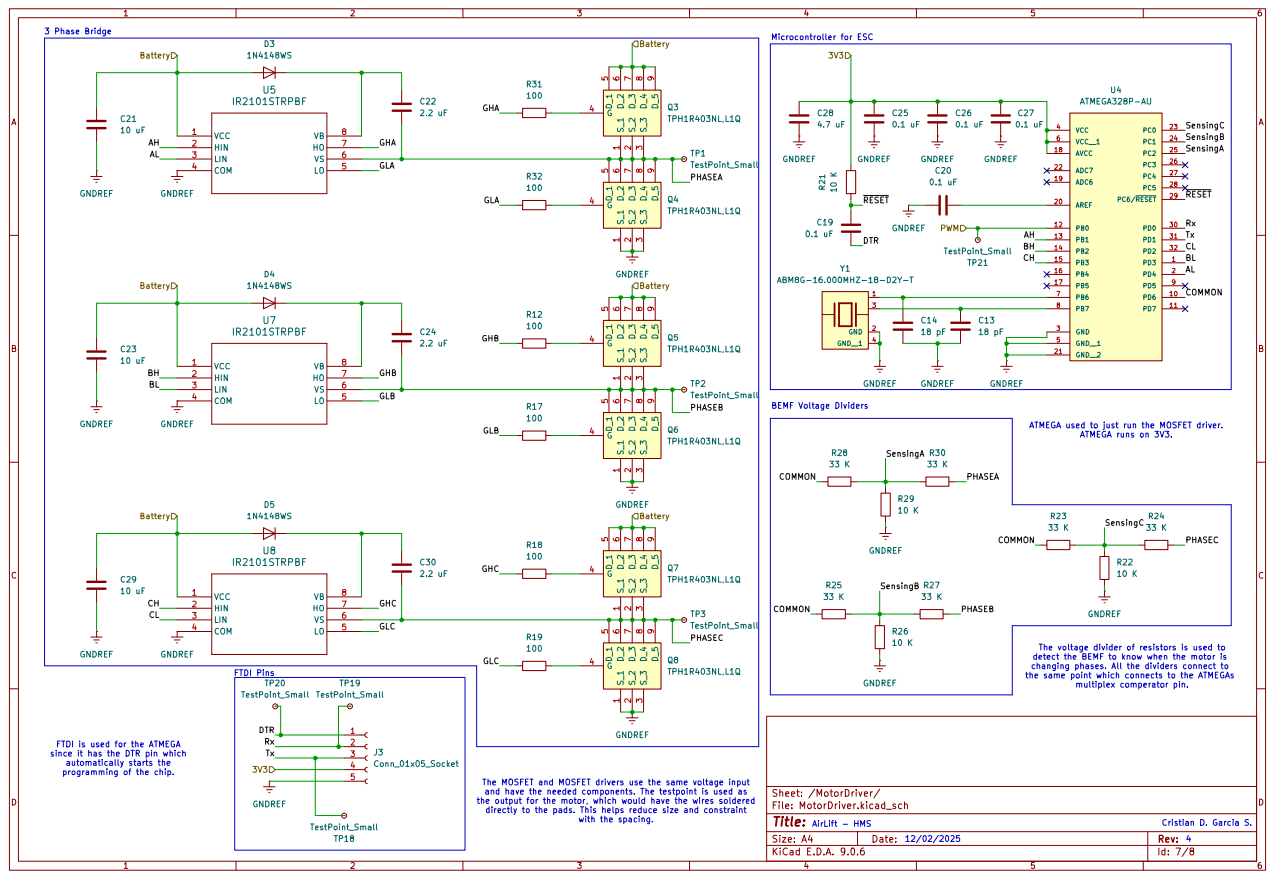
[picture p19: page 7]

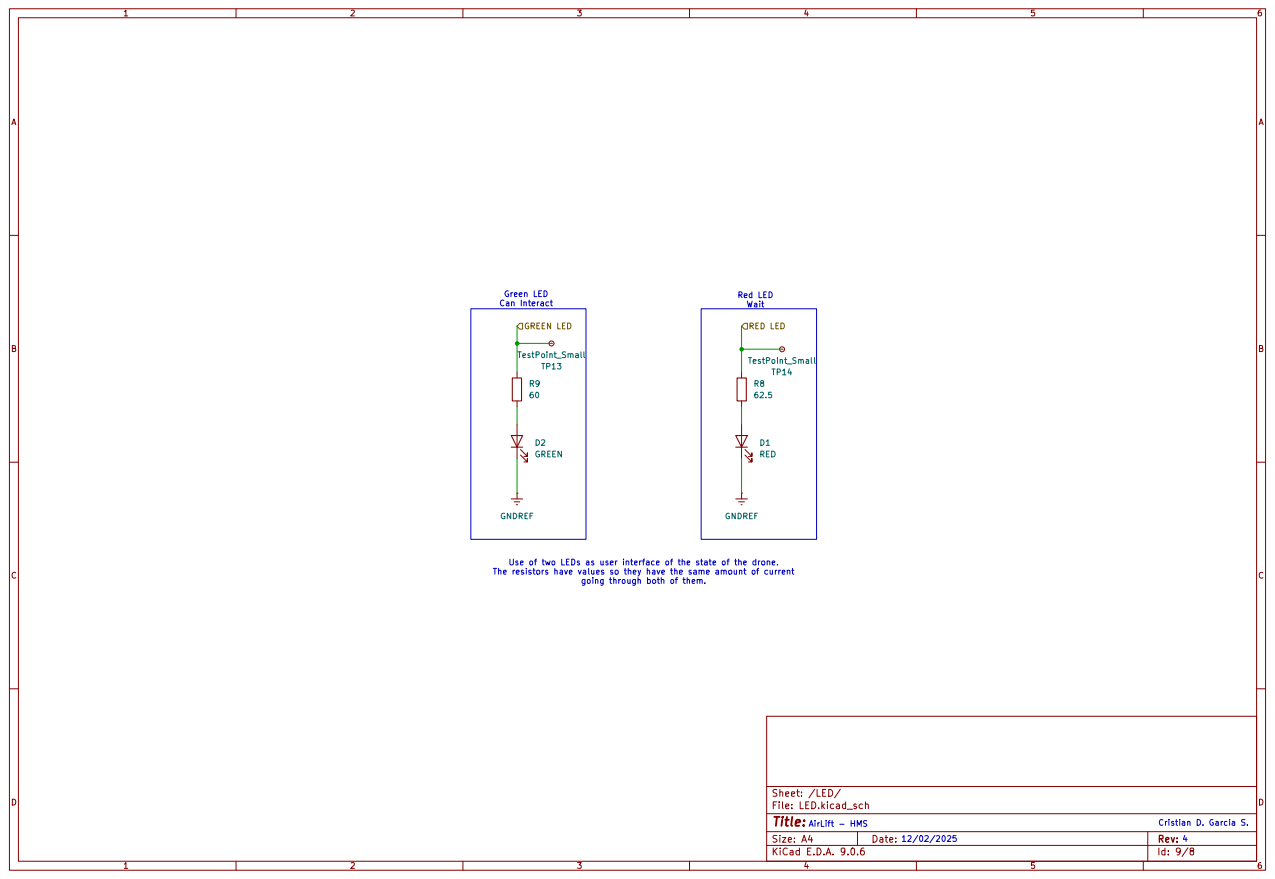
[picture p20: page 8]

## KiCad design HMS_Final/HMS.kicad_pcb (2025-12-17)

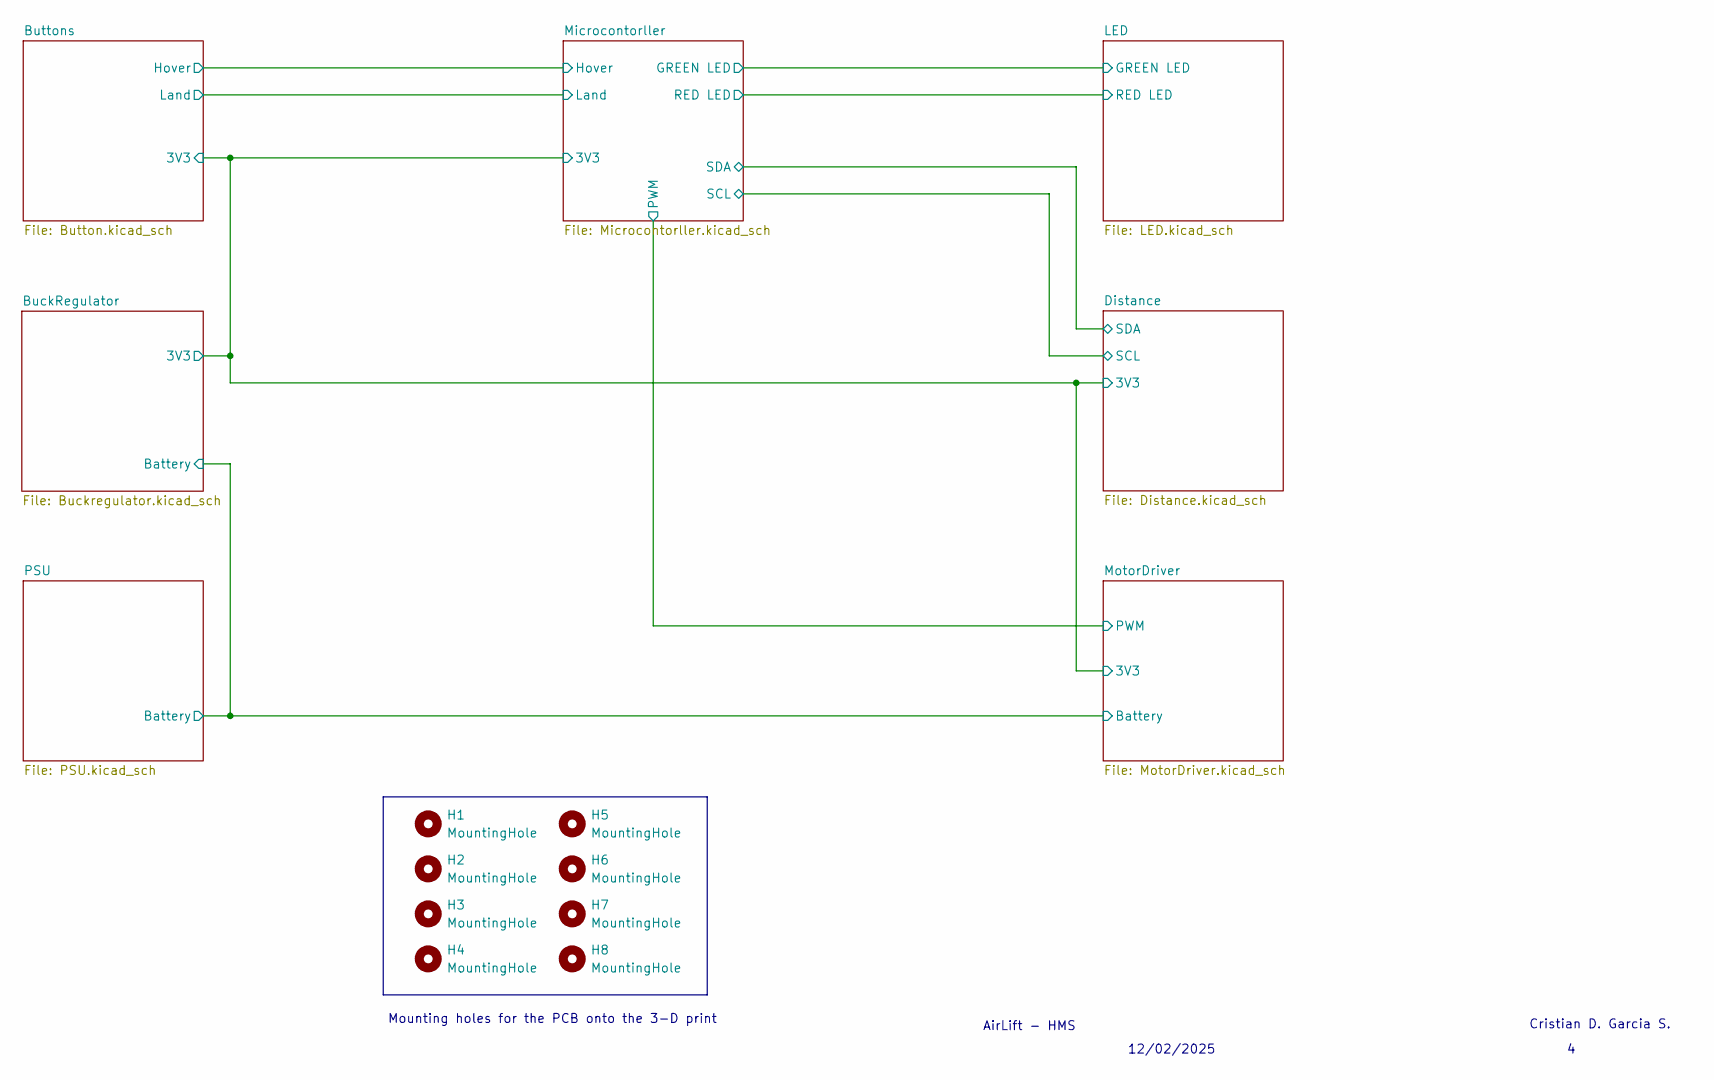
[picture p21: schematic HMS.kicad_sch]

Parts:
H1, H2, H3, H4, H5, H6, H7, H8: MountingHole; MountingHole_3.2mm_M3

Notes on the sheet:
Mounting holes for the PCB onto the 3-D print
AirLift - HMS
12/02/2025
Cristian D. Garcia S.

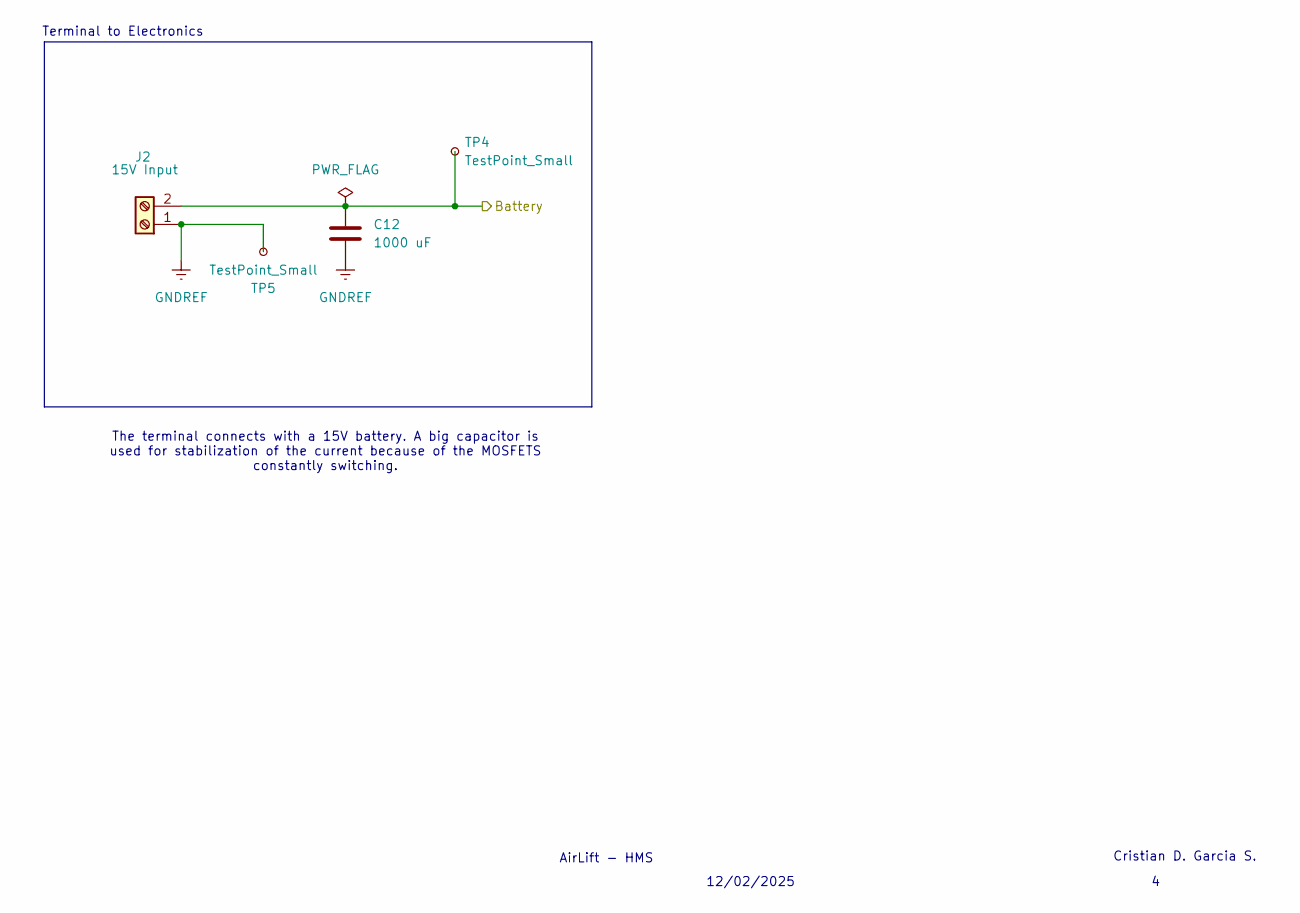
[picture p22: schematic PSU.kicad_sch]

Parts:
C12: 1000 uF; CP_Radial_D8.0mm_P3.50mm; MPN UVR1E102MPD
J2: 15V Input; AMASS_XT30U-F_1x02_P5.0mm_Vertical; MPN N/A
TP4, TP5: TestPoint_Small; TestPoint_Pad_D1.0mm

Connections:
/BuckRegulator/Battery: C12.1, J2.2, TP4.1; also elsewhere on the board
GNDREF: C12.2, J2.1, TP5.1; also elsewhere on the board

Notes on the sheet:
12/02/2025
Cristian D. Garcia S.
Terminal to Electronics
AirLift - HMS
The terminal connects with a 15V battery. A big capacitor is used for stabilization of the current because of the MOSFETS constantly switching.

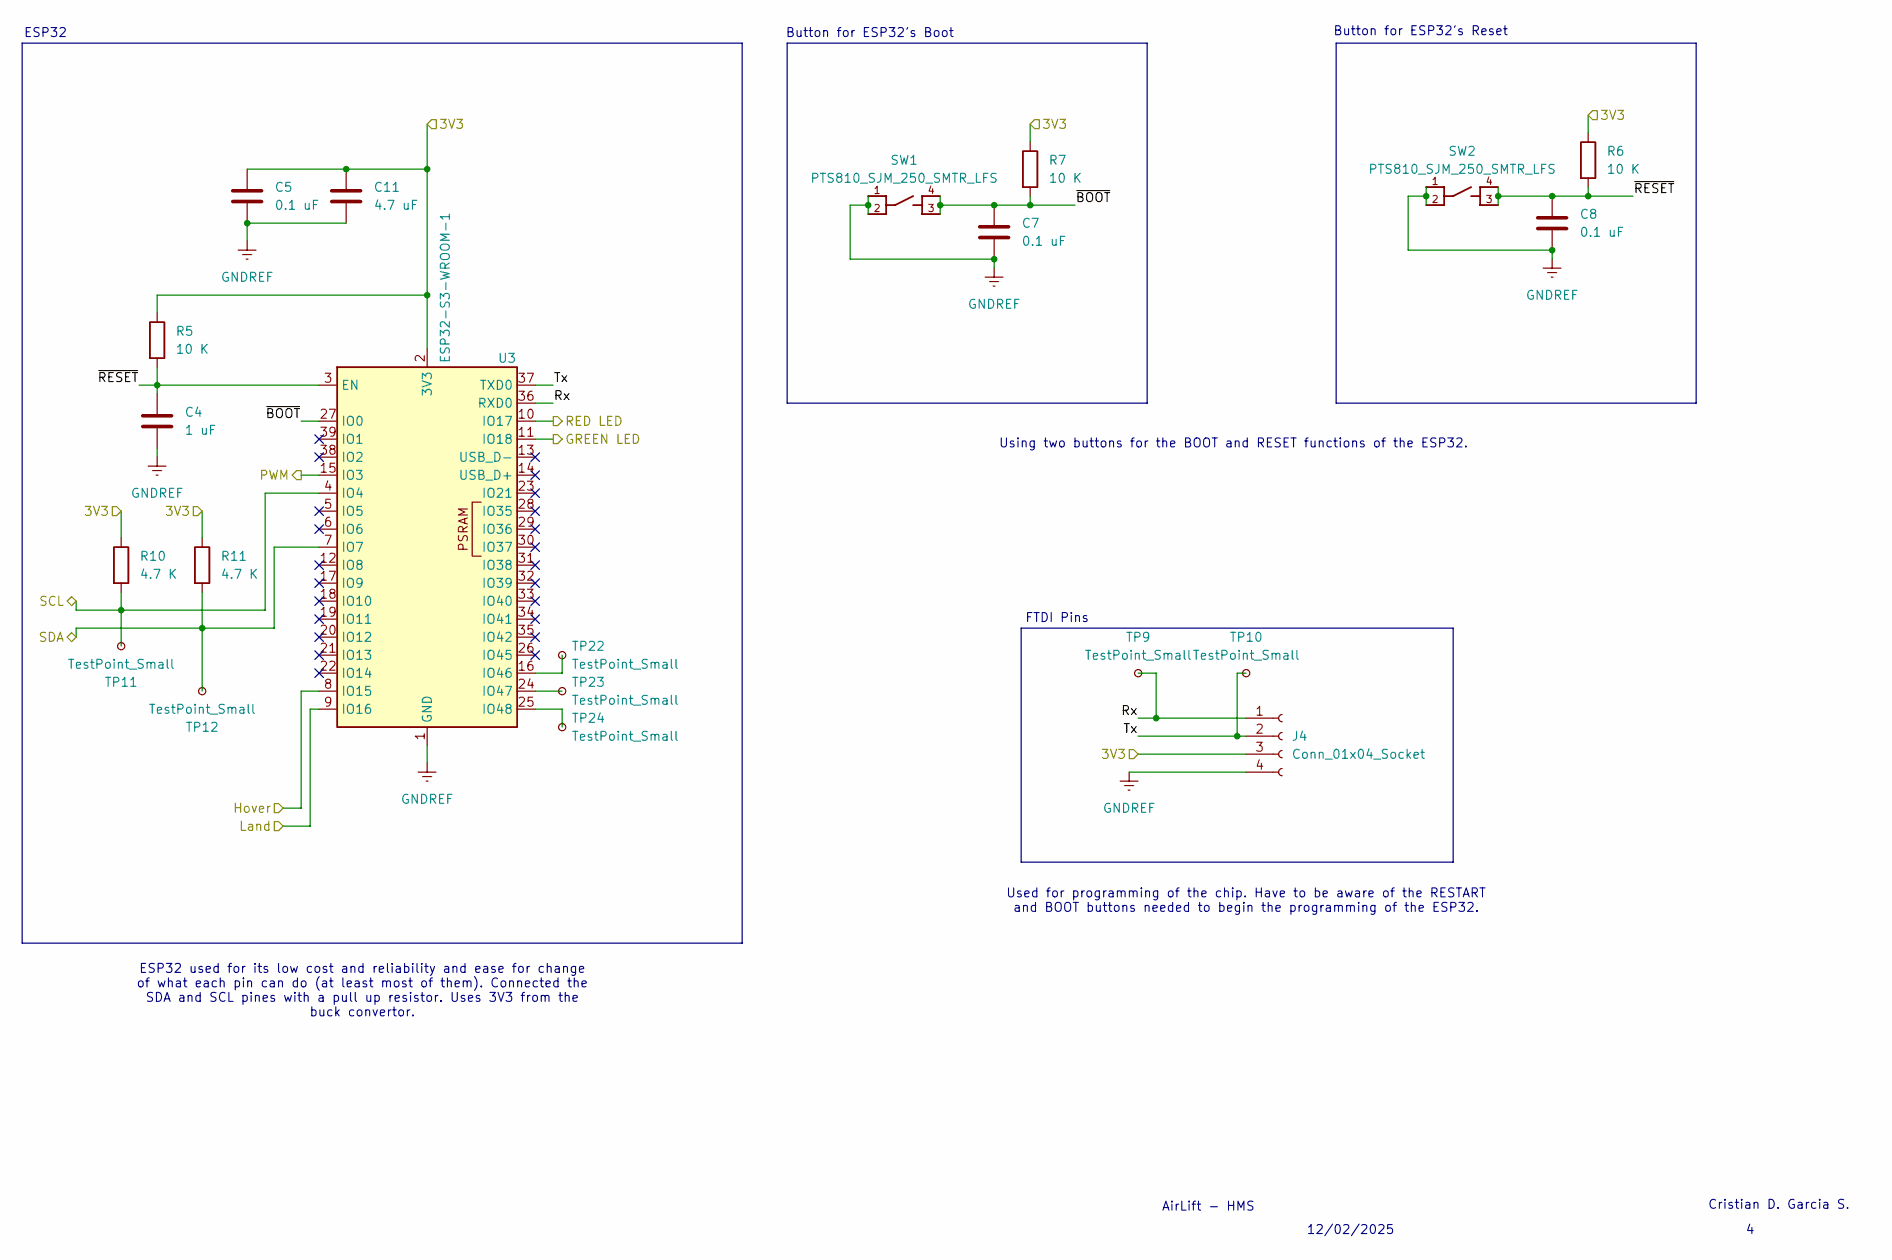
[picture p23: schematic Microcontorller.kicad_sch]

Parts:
C4: 1 uF; C_0805_2012Metric_Pad1.18x1.45mm_HandSolder; MPN C0805C105K4RACTU
C5, C7, C8: 0.1 uF; C_0805_2012Metric_Pad1.18x1.45mm_HandSolder; MPN C0805C104K4RACTU
C11: 4.7 uF; C_0805_2012Metric_Pad1.18x1.45mm_HandSolder; MPN CL21B475KOFNFNE
J4: Conn_01x04_Socket; PinSocket_1x04_P2.54mm_Vertical; MPN N/A
R5, R6, R7: 10 K; R_0805_2012Metric_Pad1.20x1.40mm_HandSolder; MPN RR1220P-103-D
R10, R11: 4.7 K; R_0805_2012Metric_Pad1.20x1.40mm_HandSolder; MPN CRCW08054K70FKEAC
SW1, SW2: PTS810_SJM_250_SMTR_LFS; SW_PTS810_SJM_250_SMTR_LFS; MPN PTS810SJS250SMTR LFS
TP9, TP10, TP11, TP12, TP22, TP23, TP24: TestPoint_Small; TestPoint_Pad_D1.0mm
U3: ESP32-S3-WROOM-1; MPN ESP32-S3-WROOM-1-N4

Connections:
/BuckRegulator/3V3: C5.1, C11.1, J4.3, R5.1, R6.1, R7.1, R10.1, R11.1, U3.2 (3V3); also elsewhere on the board
/Buttons/Hover: U3.8 (IO15); also elsewhere on the board
/Buttons/Land: U3.9 (IO16); also elsewhere on the board
/Distance/SCL: R10.2, TP11.1, U3.4 (IO4); also elsewhere on the board
/Distance/SDA: R11.2, TP12.1, U3.7 (IO7); also elsewhere on the board
/LED/GREEN LED: U3.11 (IO18); also elsewhere on the board
/LED/RED LED: U3.10 (IO17); also elsewhere on the board
/Microcontorller/PWM: U3.15 (IO3); also elsewhere on the board
/Microcontorller/Rx: J4.1, TP9.1, U3.36 (RXD0)
/Microcontorller/Tx: J4.2, TP10.1, U3.37 (TXD0)
/Microcontorller/~BOOT: C7.1, R7.2, SW1.3, SW1.4, U3.27 (IO0)
/Microcontorller/~RESET: C4.1, C8.1, R5.2, R6.2, SW2.3, SW2.4, U3.3 (EN)
GNDREF: C4.2, C5.2, C7.2, C8.2, C11.2, J4.4, SW1.1, SW1.2, SW2.1, SW2.2, U3.1 (GND), U3.40 (GND), U3.41 (GND); also elsewhere on the board
unnamed: TP22.1, U3.16 (IO46)
unnamed: TP23.1, U3.24 (IO47)
unnamed: TP24.1, U3.25 (IO48)

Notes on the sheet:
AirLift - HMS
12/02/2025
Cristian D. Garcia S.
ESP32
Button for ESP32's Boot
Using two buttons for the BOOT and RESET functions of the ESP32.
ESP32 used for its low cost and reliability and ease for change of what each pin can do (at least most of them). Connected the SDA and SCL pines with a pull up resistor. Uses 3V3 from the buck convertor.
FTDI Pins
Button for ESP32's Reset
Used for programming of the chip. Have to be aware of the RESTART and BOOT buttons needed to begin the programming of the ESP32.

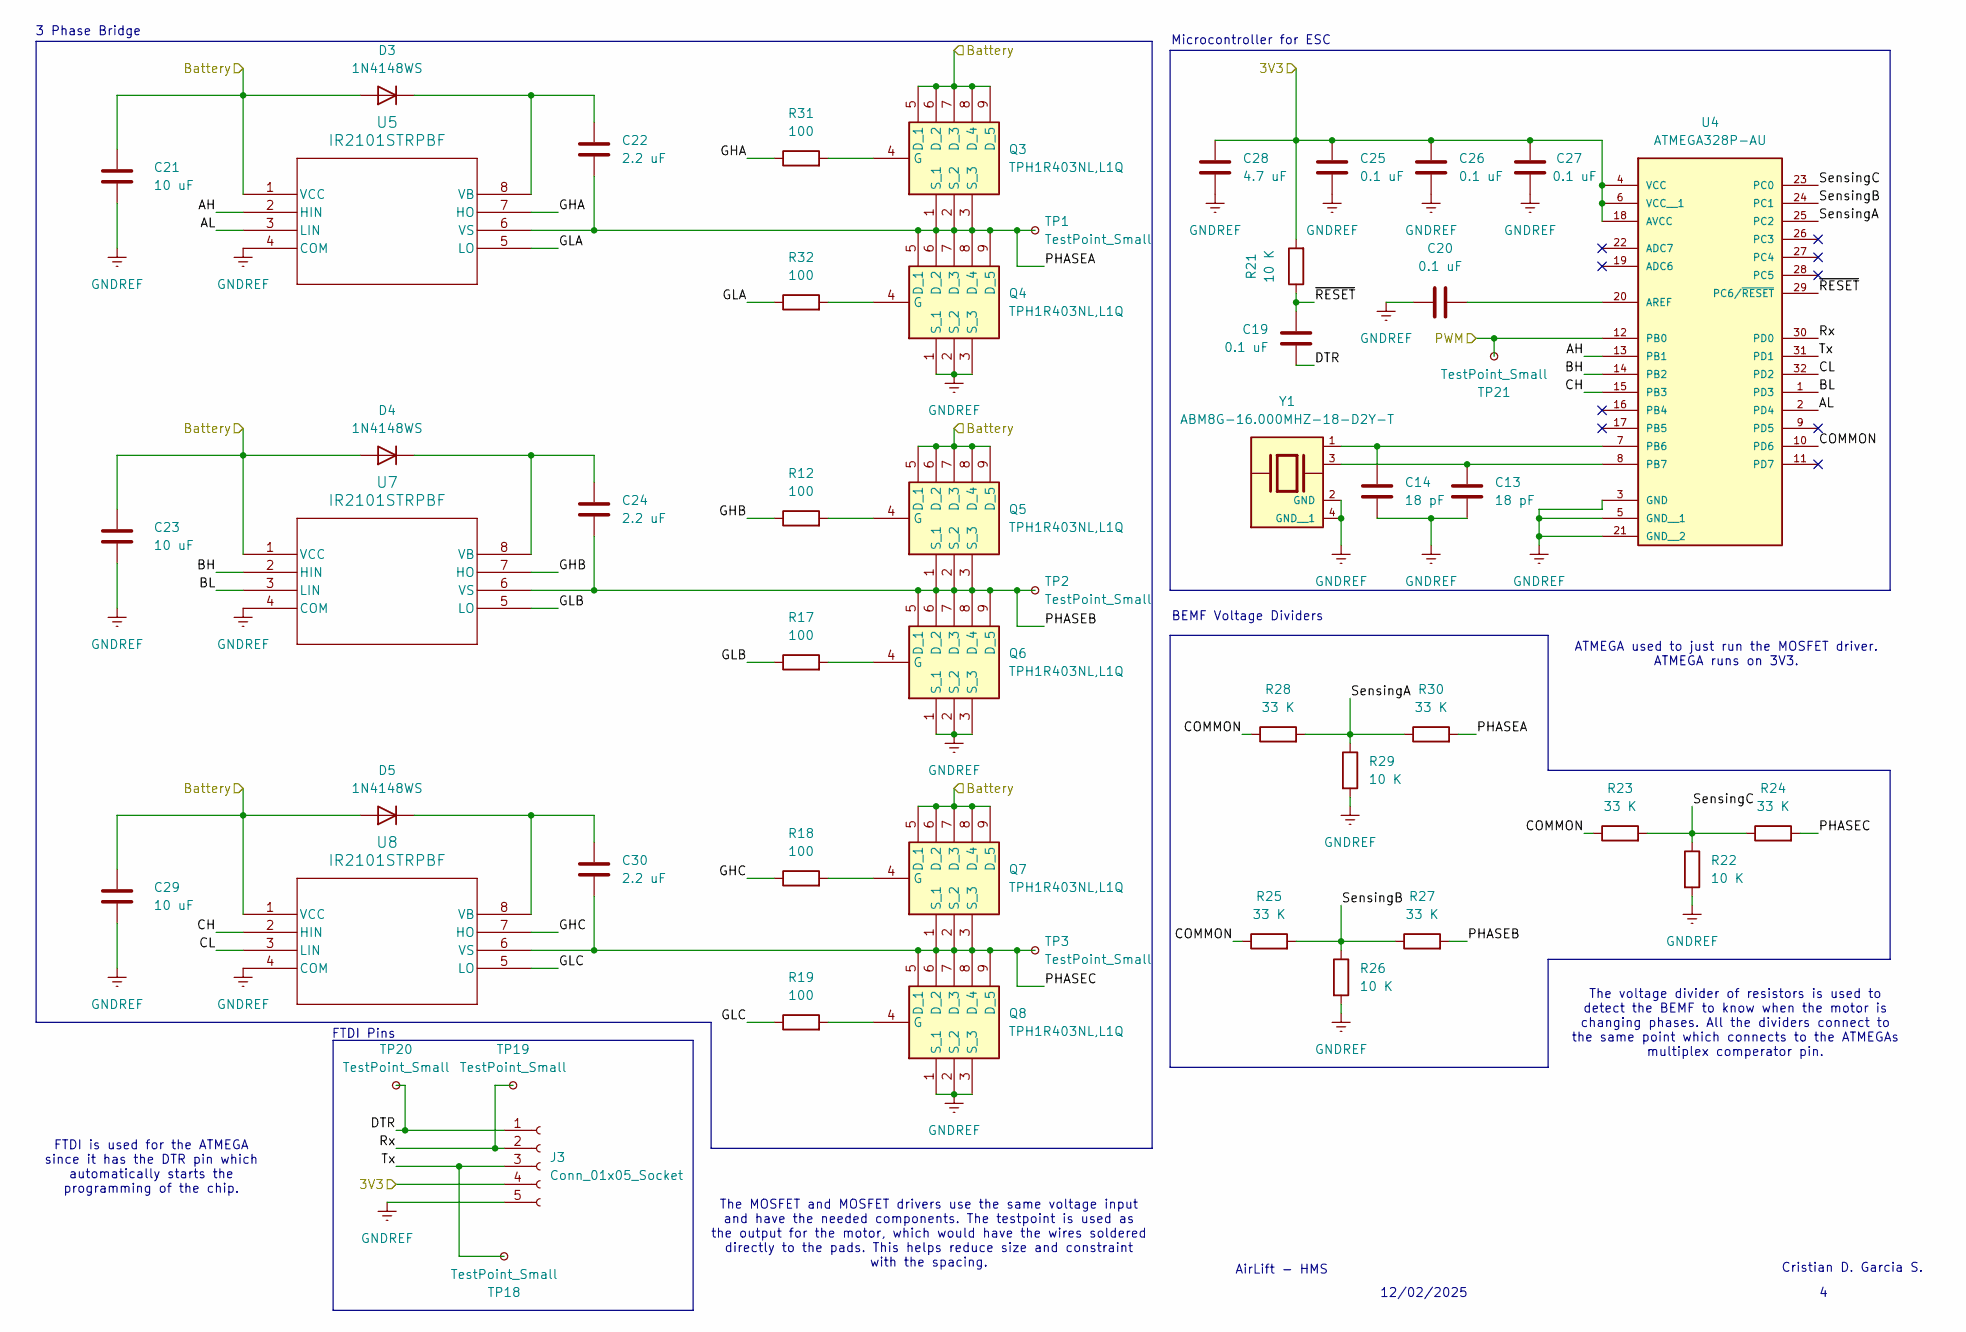
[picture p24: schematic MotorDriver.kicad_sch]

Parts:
C13, C14: 18 pF; C_0805_2012Metric_Pad1.18x1.45mm_HandSolder; MPN C0805C180G4HACTU
C19, C20, C25, C26, C27: 0.1 uF; C_0805_2012Metric_Pad1.18x1.45mm_HandSolder; MPN C0805C104K4RACTU
C21, C23, C29: 10 uF; C_0805_2012Metric_Pad1.18x1.45mm_HandSolder; MPN CL21A106KOQNNNE
C22, C24, C30: 2.2 uF; C_0805_2012Metric_Pad1.18x1.45mm_HandSolder; MPN GRM21BR71C225KA12L
C28: 4.7 uF; C_0805_2012Metric_Pad1.18x1.45mm_HandSolder; MPN CL21B475KOFNFNE
D3, D4, D5: 1N4148WS; SODFL2512X100N
J3: Conn_01x05_Socket; PinSocket_1x05_P2.54mm_Vertical; MPN N/A
Q3, Q4, Q5, Q6, Q7, Q8: TPH1R403NL,L1Q; TPH1R403NLL1Q; Mouser Part Number 757-TPH1R403NLL1Q
R12, R17, R18, R19, R31, R32: 100; R_0805_2012Metric_Pad1.20x1.40mm_HandSolder; MPN ERA-6AEB101V
R21, R22, R26, R29: 10 K; R_0805_2012Metric_Pad1.20x1.40mm_HandSolder; MPN RR1220P-103-D
R23, R24, R25, R27, R28, R30: 33 K; R_0805_2012Metric_Pad1.20x1.40mm_HandSolder; MPN RC0805FR-0733KL
TP1, TP2, TP3: TestPoint_Small; TestPoint_Pad_1.0x1.0mm; MPN N/A
TP18, TP19, TP20, TP21: TestPoint_Small; TestPoint_Pad_D1.0mm
U4: ATMEGA328P-AU; QFP80P900X900X120-32N; PARTREV 8271A
U5, U7, U8: IR2101STRPBF; SO8N_INF; MPN IR2101STRPBF
Y1: ABM8G-16.000MHZ-18-D2Y-T; XTAL_ABM8G-16.000MHZ-18-D2Y-T; PARTREV 08.13.15

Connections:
/BuckRegulator/3V3: C25.1, C26.1, C27.2, C28.1, J3.4, R21.2, U4.4 (VCC), U4.6 (VCC__1), U4.18 (AVCC); also elsewhere on the board
/BuckRegulator/Battery: C21.1, C23.1, C29.1, D3.2 (A), D4.2 (A), D5.2 (A), Q3.5 (D_1), Q3.6 (D_2), Q3.7 (D_3), Q3.8 (D_4), Q3.9 (D_5), Q5.5 (D_1), Q5.6 (D_2), Q5.7 (D_3), Q5.8 (D_4), Q5.9 (D_5), Q7.5 (D_1), Q7.6 (D_2), Q7.7 (D_3), Q7.8 (D_4), Q7.9 (D_5), U5.1 (VCC), U7.1 (VCC), U8.1 (VCC); also elsewhere on the board
/Microcontorller/PWM: TP21.1, U4.12 (PB0); also elsewhere on the board
/MotorDriver/AH: U4.13 (PB1), U5.2 (HIN)
/MotorDriver/AL: U4.2 (PD4), U5.3 (LIN)
/MotorDriver/BH: U4.14 (PB2), U7.2 (HIN)
/MotorDriver/BL: U4.1 (PD3), U7.3 (LIN)
/MotorDriver/CH: U4.15 (PB3), U8.2 (HIN)
/MotorDriver/CL: U4.32 (PD2), U8.3 (LIN)
/MotorDriver/COMMON: R23.1, R25.1, R28.1, U4.10 (PD6)
/MotorDriver/DTR: C19.1, J3.1, TP20.1
/MotorDriver/GHA: R31.1, U5.7 (HO)
/MotorDriver/GHB: R12.1, U7.7 (HO)
/MotorDriver/GHC: R18.1, U8.7 (HO)
/MotorDriver/GLA: R32.1, U5.5 (LO)
/MotorDriver/GLB: R17.1, U7.5 (LO)
/MotorDriver/GLC: R19.1, U8.5 (LO)
/MotorDriver/PHASEA: C22.1, Q3.1 (S_1), Q3.2 (S_2), Q3.3 (S_3), Q4.5 (D_1), Q4.6 (D_2), Q4.7 (D_3), Q4.8 (D_4), Q4.9 (D_5), R30.2, TP1.1, U5.6 (VS)
/MotorDriver/PHASEB: C24.1, Q5.1 (S_1), Q5.2 (S_2), Q5.3 (S_3), Q6.5 (D_1), Q6.6 (D_2), Q6.7 (D_3), Q6.8 (D_4), Q6.9 (D_5), R27.2, TP2.1, U7.6 (VS)
/MotorDriver/PHASEC: C30.1, Q7.1 (S_1), Q7.2 (S_2), Q7.3 (S_3), Q8.5 (D_1), Q8.6 (D_2), Q8.7 (D_3), Q8.8 (D_4), Q8.9 (D_5), R24.2, TP3.1, U8.6 (VS)
/MotorDriver/Rx: J3.2, TP19.1, U4.30 (PD0)
/MotorDriver/SensingA: R28.2, R29.1, R30.1, U4.25 (PC2)
/MotorDriver/SensingB: R25.2, R26.1, R27.1, U4.24 (PC1)
/MotorDriver/SensingC: R22.1, R23.2, R24.1, U4.23 (PC0)
/MotorDriver/Tx: J3.3, TP18.1, U4.31 (PD1)
/MotorDriver/~RESET: C19.2, R21.1, U4.29 (PC6/~RESET)
GNDREF: C13.2, C14.2, C20.2, C21.2, C23.2, C25.2, C26.2, C27.1, C28.2, C29.2, J3.5, Q4.1 (S_1), Q4.2 (S_2), Q4.3 (S_3), Q6.1 (S_1), Q6.2 (S_2), Q6.3 (S_3), Q8.1 (S_1), Q8.2 (S_2), Q8.3 (S_3), R22.2, R26.2, R29.2, U4.3 (GND), U4.5 (GND__1), U4.21 (GND__2), U5.4 (COM), U7.4 (COM), U8.4 (COM), Y1.2 (GND), Y1.4 (GND__1); also elsewhere on the board
unnamed: C22.2, D3.1 (K), U5.8 (VB)
unnamed: C24.2, D4.1 (K), U7.8 (VB)
unnamed: C30.2, D5.1 (K), U8.8 (VB)
unnamed: Q3.4 (G), R31.2
unnamed: Q4.4 (G), R32.2
unnamed: Q5.4 (G), R12.2
unnamed: Q6.4 (G), R17.2
unnamed: Q7.4 (G), R18.2
unnamed: Q8.4 (G), R19.2
unnamed: C20.1, U4.20 (AREF)
unnamed: C14.1, U4.7 (PB6), Y1.1
unnamed: C13.1, U4.8 (PB7), Y1.3

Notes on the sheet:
Cristian D. Garcia S.
12/02/2025
The voltage divider of resistors is used to detect the BEMF to know when the motor is changing phases. All the dividers connect to the same point which connects to the ATMEGAs multiplex comperator pin.
FTDI is used for the ATMEGA since it has the DTR pin which automatically starts the programming of the chip.
ATMEGA used to just run the MOSFET driver. ATMEGA runs on 3V3.
FTDI Pins
Microcontroller for ESC
BEMF Voltage Dividers
The MOSFET and MOSFET drivers use the same voltage input and have the needed components. The testpoint is used as the output for the motor, which would have the wires soldered directly to the pads. This helps reduce size and constraint with the spacing.
3 Phase Bridge
AirLift - HMS

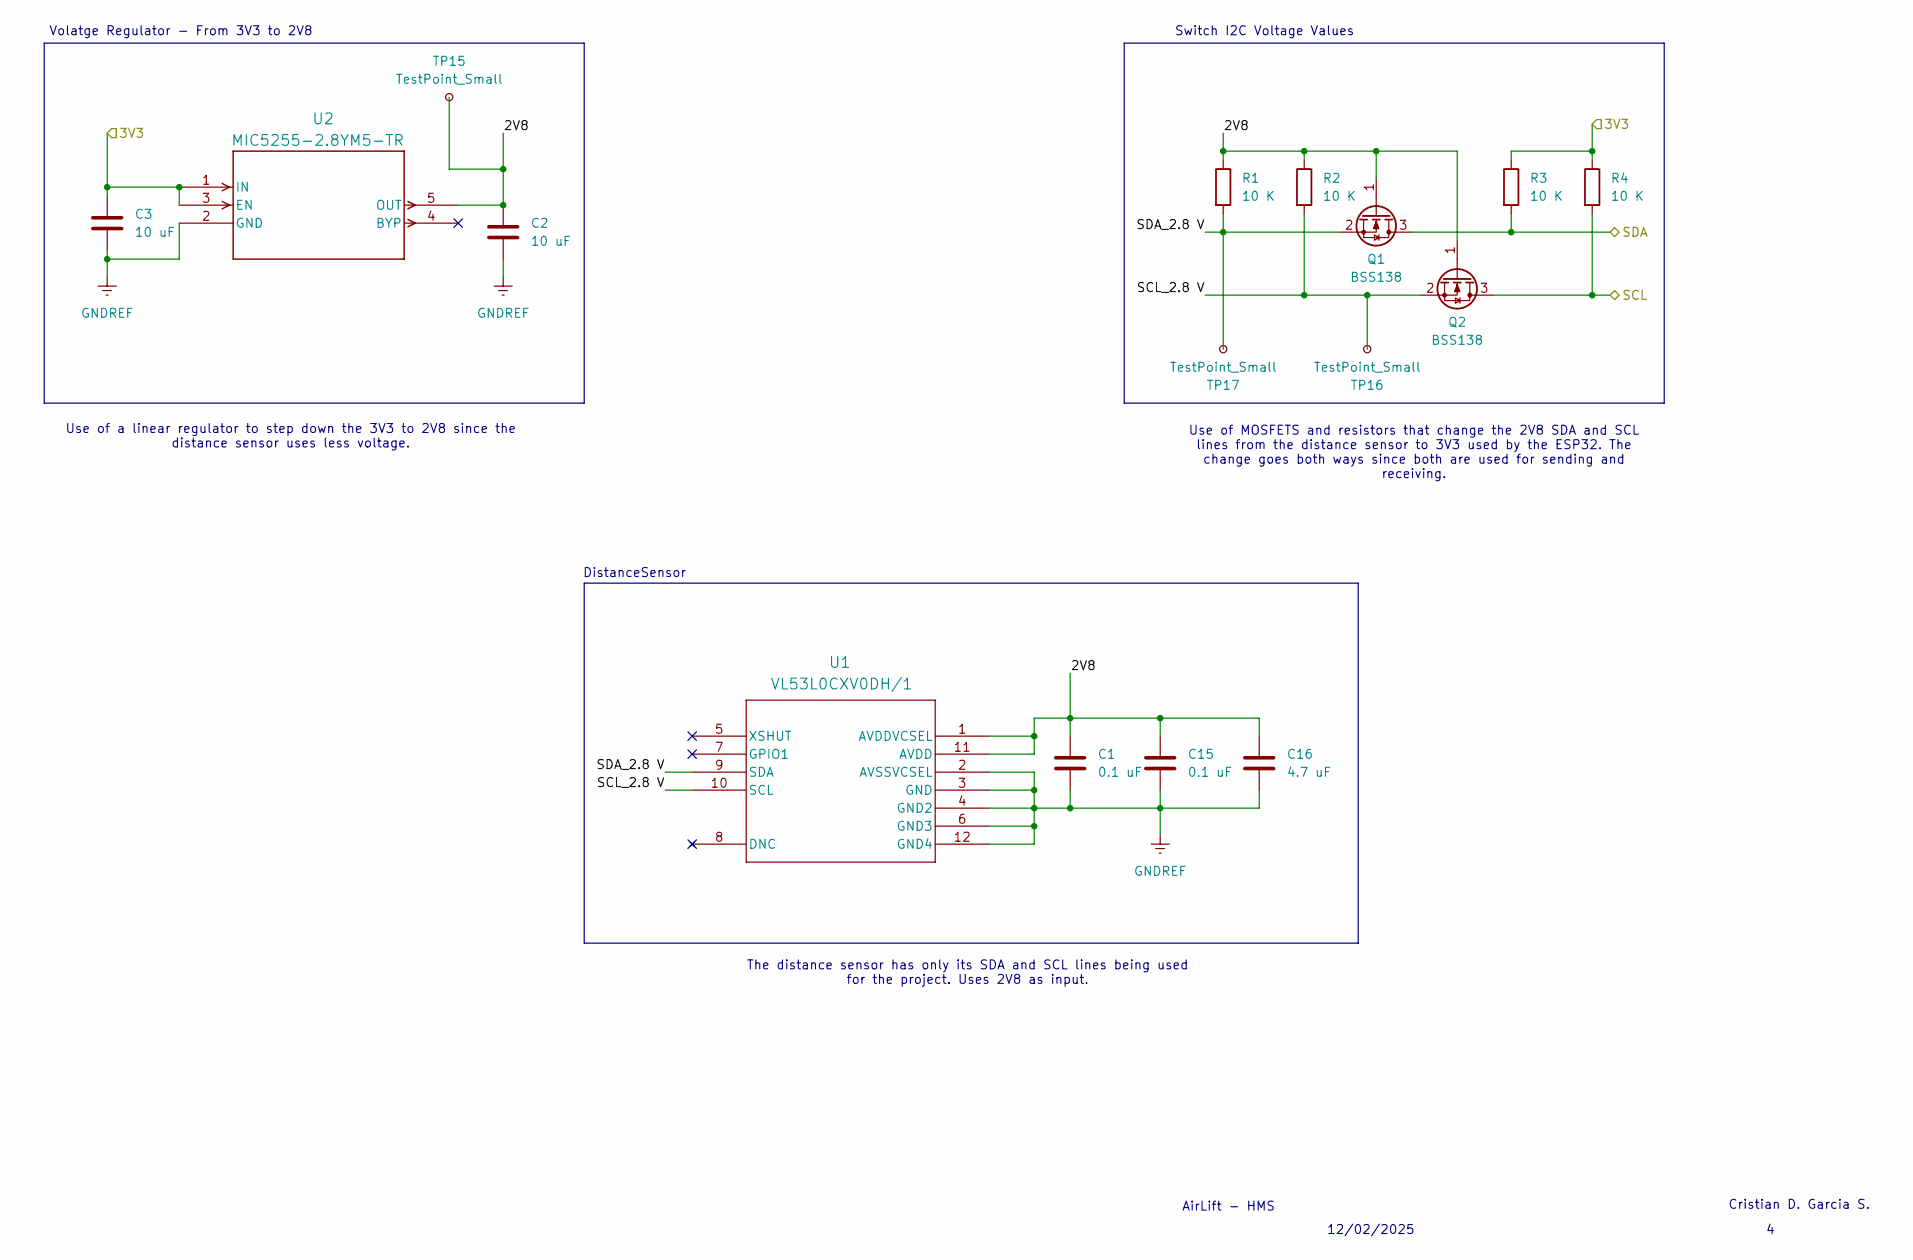
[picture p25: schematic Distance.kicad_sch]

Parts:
C1, C15: 0.1 uF; C_0805_2012Metric_Pad1.18x1.45mm_HandSolder; MPN C0805C104K4RACTU
C2, C3: 10 uF; C_0805_2012Metric_Pad1.18x1.45mm_HandSolder; MPN CL21A106KOQNNNE
C16: 4.7 uF; C_0805_2012Metric_Pad1.18x1.45mm_HandSolder; MPN CL21B475KOFNFNE
Q1, Q2: BSS138; SOT-23-3_1P4X3P040_ONS; MPN BSS138
R1, R2, R3, R4: 10 K; R_0805_2012Metric_Pad1.20x1.40mm_HandSolder; MPN RR1220P-103-D
TP15, TP16, TP17: TestPoint_Small; TestPoint_Pad_D1.0mm
U1: VL53L0CXV0DH/1; LGA12_STM; MPN VL53L0CXV0DH/1
U2: MIC5255-2.8YM5-TR; SOT-23-5_M5_MCH; MPN MIC5255-2.8YM5-TR

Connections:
/BuckRegulator/3V3: C3.1, R3.1, R4.1, U2.1 (IN), U2.3 (EN); also elsewhere on the board
/Distance/2V8: C1.1, C2.1, C15.1, C16.1, Q1.1 (G), Q2.1 (G), R1.1, R2.1, TP15.1, U1.1 (AVDDVCSEL), U1.11 (AVDD), U2.5 (OUT)
/Distance/SCL: Q2.3 (D), R4.2; also elsewhere on the board
/Distance/SCL_2.8 V: Q2.2 (S), R2.2, TP16.1, U1.10 (SCL)
/Distance/SDA: Q1.3 (D), R3.2; also elsewhere on the board
/Distance/SDA_2.8 V: Q1.2 (S), R1.2, TP17.1, U1.9 (SDA)
GNDREF: C1.2, C2.2, C3.2, C15.2, C16.2, U1.2 (AVSSVCSEL), U1.3 (GND), U1.4 (GND2), U1.6 (GND3), U1.12 (GND4), U2.2 (GND); also elsewhere on the board

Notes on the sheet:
Volatge Regulator - From 3V3 to 2V8
Use of a linear regulator to step down the 3V3 to 2V8 since the distance sensor uses less voltage.
Use of MOSFETS and resistors that change the 2V8 SDA and SCL lines from the distance sensor to 3V3 used by the ESP32. The change goes both ways since both are used for sending and receiving.
AirLift - HMS
12/02/2025
Cristian D. Garcia S.
Switch I2C Voltage Values
DistanceSensor
The distance sensor has only its SDA and SCL lines being used for the project. Uses 2V8 as input.

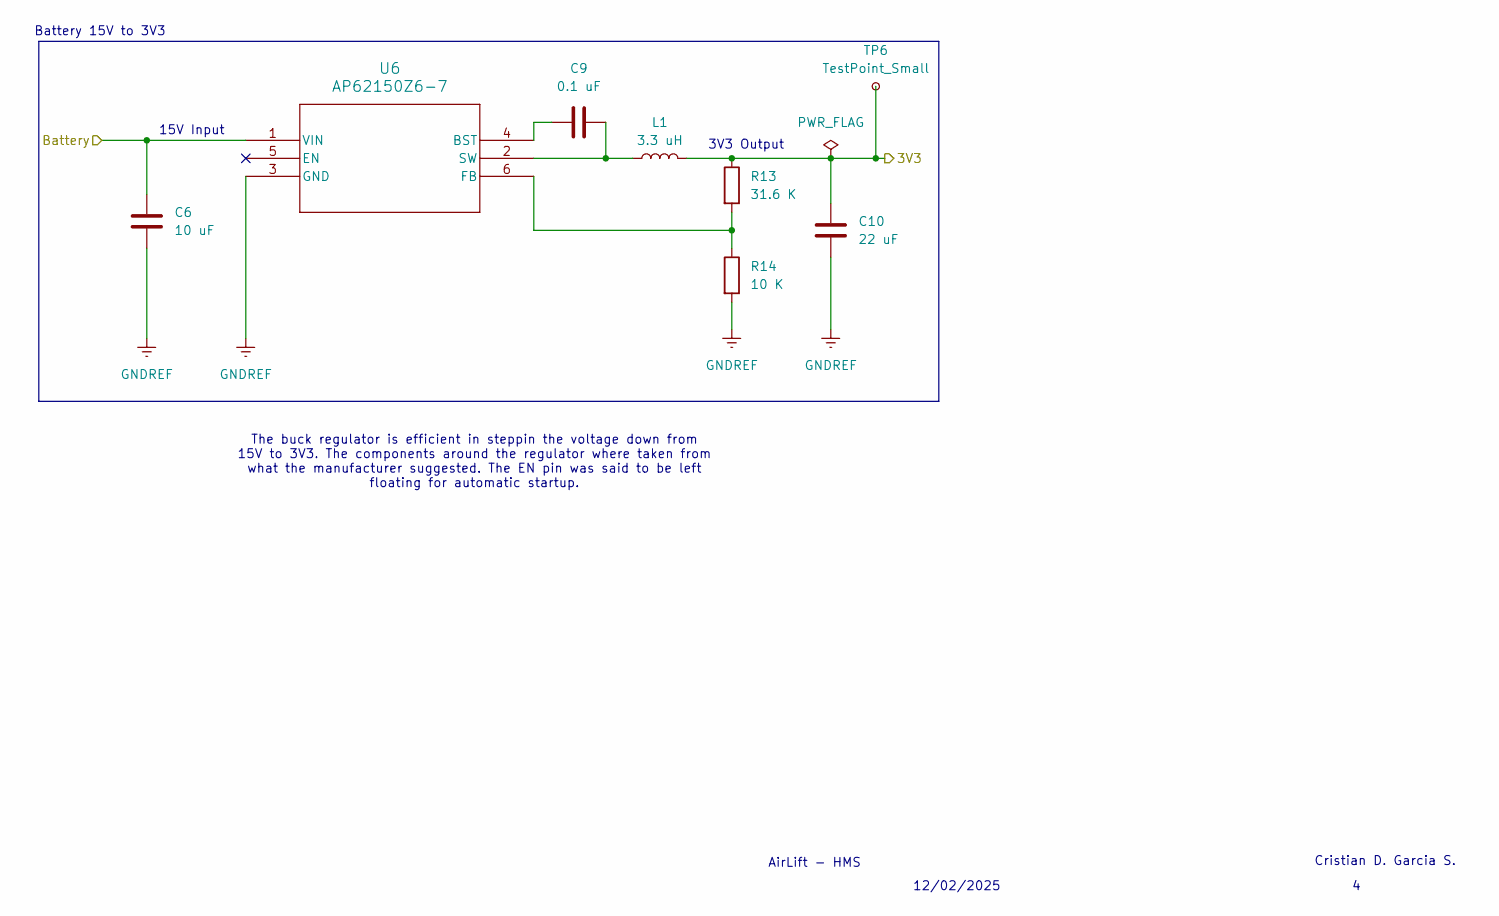
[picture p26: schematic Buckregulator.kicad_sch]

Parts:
C6: 10 uF; C_0805_2012Metric_Pad1.18x1.45mm_HandSolder; MPN CL21A106KOQNNNE
C9: 0.1 uF; C_0805_2012Metric_Pad1.18x1.45mm_HandSolder; MPN C0805C104K4RACTU
C10: 22 uF; C_0805_2012Metric_Pad1.18x1.45mm_HandSolder; MPN CL21A226MOQNNNE
L1: 3.3 uH; L_0805_2012Metric_Pad1.15x1.40mm_HandSolder; MPN MLZ2012N3R3LT000
R13: 31.6 K; R_0805_2012Metric_Pad1.20x1.40mm_HandSolder; MPN ERA-6AEB3162V
R14: 10 K; R_0805_2012Metric_Pad1.20x1.40mm_HandSolder; MPN RR1220P-103-D
TP6: TestPoint_Small; TestPoint_Pad_D1.0mm
U6: AP62150Z6-7; SOT563_DIO; MPN AP62150Z6-7

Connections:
/BuckRegulator/3V3: C10.2, L1.2, R13.1, TP6.1; also elsewhere on the board
/BuckRegulator/Battery: C6.1, U6.1 (VIN); also elsewhere on the board
GNDREF: C6.2, C10.1, R14.2, U6.3 (GND); also elsewhere on the board
unnamed: C9.1, U6.4 (BST)
unnamed: R13.2, R14.1, U6.6 (FB)
unnamed: C9.2, L1.1, U6.2 (SW)

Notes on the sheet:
12/02/2025
AirLift - HMS
Cristian D. Garcia S.
Battery 15V to 3V3
15V Input
The buck regulator is efficient in steppin the voltage down from 15V to 3V3. The components around the regulator where taken from what the manufacturer suggested. The EN pin was said to be left floating for automatic startup.
3V3 Output

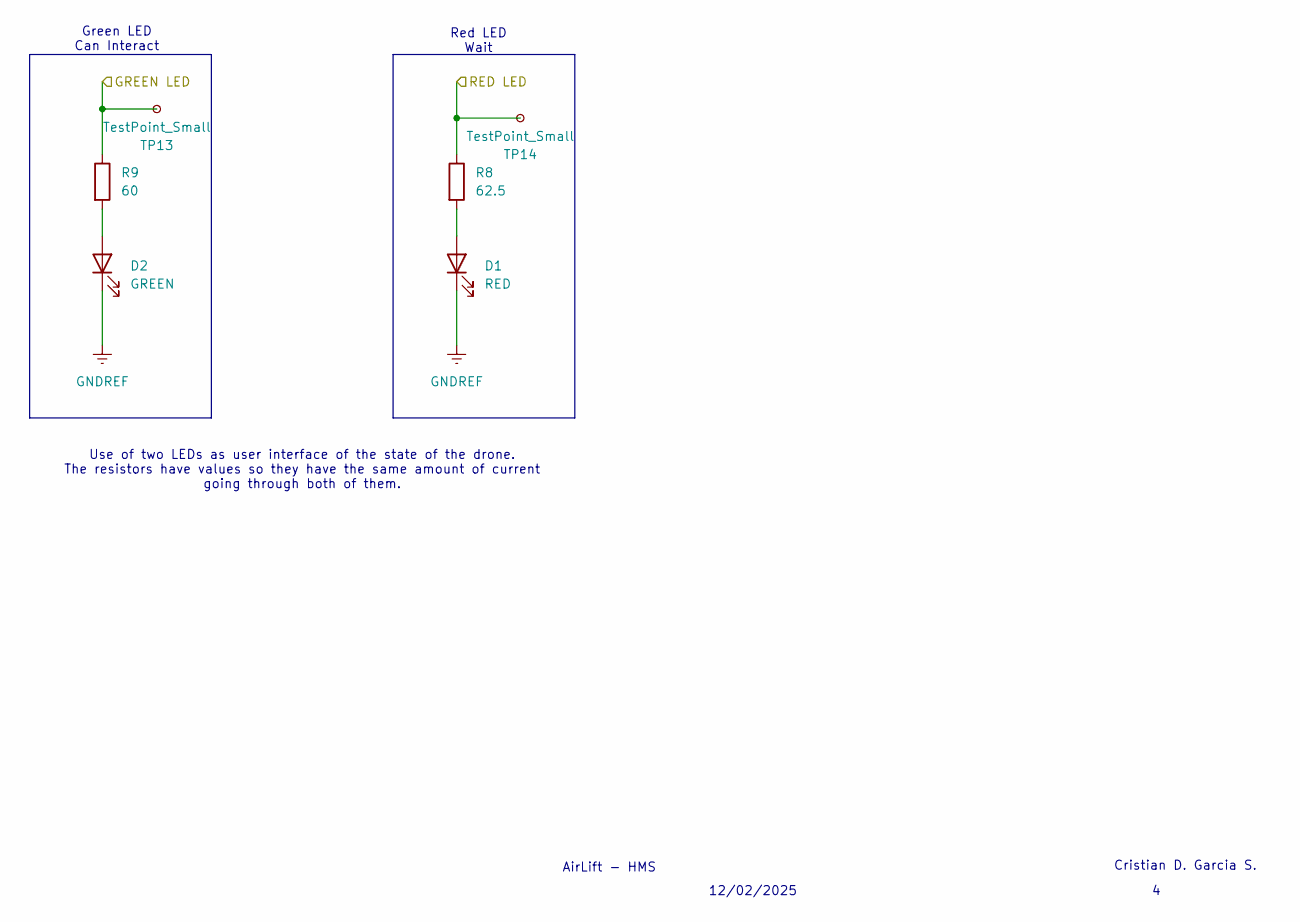
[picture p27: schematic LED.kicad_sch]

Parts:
D1: RED; LED_D5.0mm; MPN N/A
D2: GREEN; LED_D5.0mm; MPN N/A
R8: 62.5; R_0805_2012Metric_Pad1.20x1.40mm_HandSolder; MPN ERA-6AEB101V
R9: 60; R_0805_2012Metric_Pad1.20x1.40mm_HandSolder; MPN ERA-6AEB101V
TP13, TP14: TestPoint_Small; TestPoint_Pad_D1.0mm

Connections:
/LED/GREEN LED: R9.1, TP13.1; also elsewhere on the board
/LED/RED LED: R8.1, TP14.1; also elsewhere on the board
GNDREF: D1.1 (K), D2.1 (K); also elsewhere on the board
unnamed: D1.2 (A), R8.2
unnamed: D2.2 (A), R9.2

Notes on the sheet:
Green LED Can Interact
12/02/2025
Cristian D. Garcia S.
AirLift - HMS
Use of two LEDs as user interface of the state of the drone. The resistors have values so they have the same amount of current going through both of them.
Red LED Wait

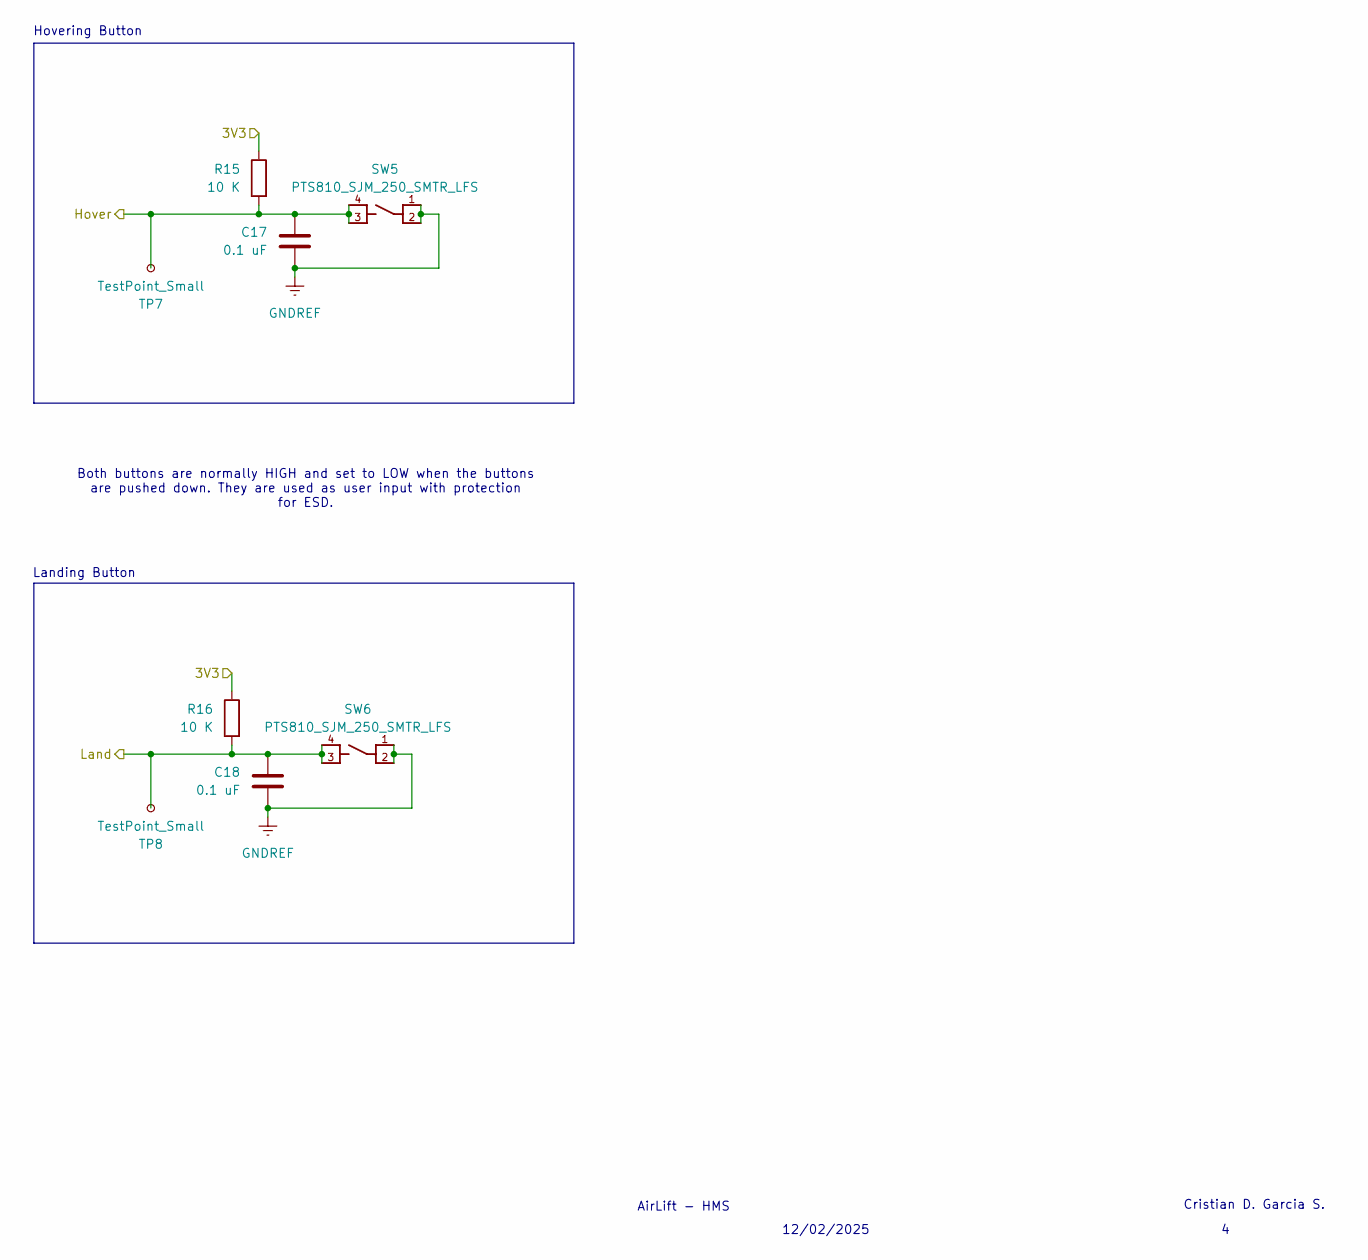
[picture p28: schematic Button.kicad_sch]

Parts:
C17, C18: 0.1 uF; C_0805_2012Metric_Pad1.18x1.45mm_HandSolder; MPN C0805C104K4RACTU
R15, R16: 10 K; R_0805_2012Metric_Pad1.20x1.40mm_HandSolder; MPN RR1220P-103-D
SW5, SW6: PTS810_SJM_250_SMTR_LFS; SW_PTS810_SJM_250_SMTR_LFS; MPN PTS810SJS250SMTR LFS
TP7, TP8: TestPoint_Small; TestPoint_Pad_D1.0mm

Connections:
/BuckRegulator/3V3: R15.1, R16.1; also elsewhere on the board
/Buttons/Hover: C17.1, R15.2, SW5.3, SW5.4, TP7.1; also elsewhere on the board
/Buttons/Land: C18.1, R16.2, SW6.3, SW6.4, TP8.1; also elsewhere on the board
GNDREF: C17.2, C18.2, SW5.1, SW5.2, SW6.1, SW6.2; also elsewhere on the board

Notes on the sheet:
Both buttons are normally HIGH and set to LOW when the buttons are pushed down. They are used as user input with protection for ESD.
Hovering Button
Cristian D. Garcia S.
AirLift - HMS
12/02/2025
Landing Button

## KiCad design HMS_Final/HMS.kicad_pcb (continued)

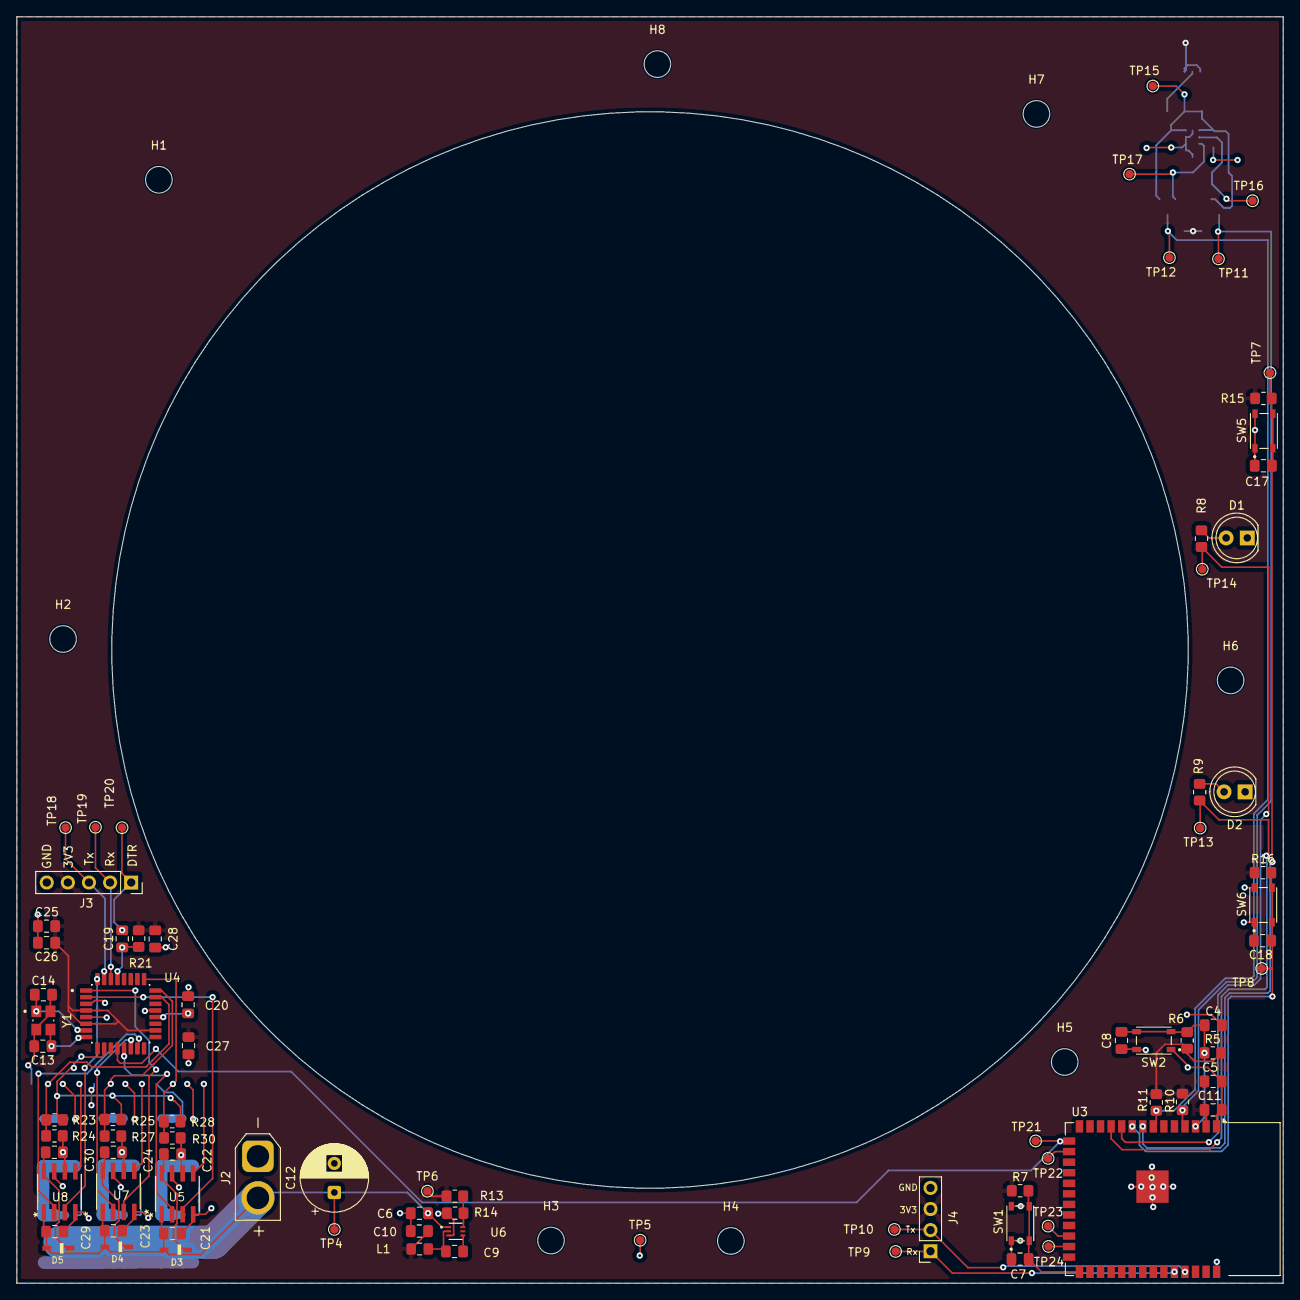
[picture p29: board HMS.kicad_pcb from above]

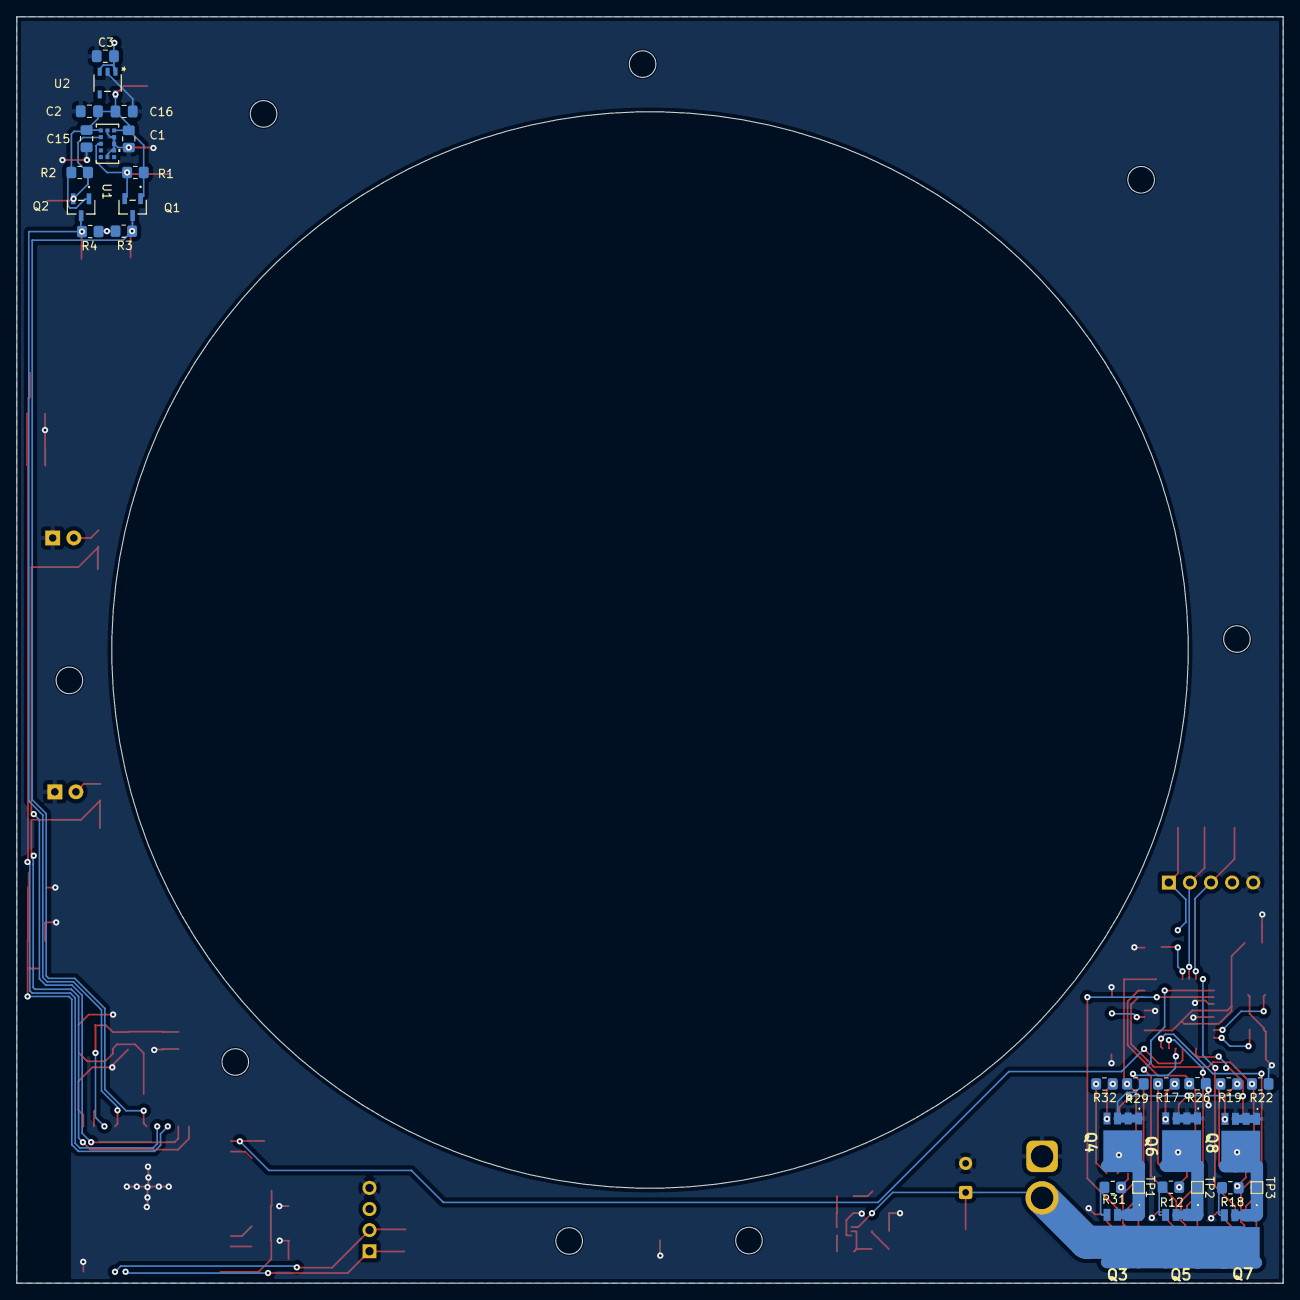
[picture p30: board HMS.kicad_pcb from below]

Board: 2 copper layers, 152.4 x 152.4 mm, 123 parts (31 on the bottom side), 60 nets.

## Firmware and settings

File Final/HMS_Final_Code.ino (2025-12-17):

#include <Adafruit_VL53L0X.h> //distance sensor library
#include <ESP32Servo.h> //servo library
#include <Wire.h> //I2C library

//Making objects of the distance and ESC
Adafruit_VL53L0X vl53lox = Adafruit_VL53L0X();
Servo speedCon;
//Pins to use when wiring
#define pin_ESC 7
#define HOVER 6
#define LAND 15
#define pin_SDA 8
#define pin_SCL 9
// Zero value for the motor
#define servoZero 1000

void setup() {

    Serial.begin(9600);
    //Two pins being used for SDA and SCL
    Wire.setPins(pin_SDA, pin_SCL);
    //Setting the pin used for ESC and max/min microseconds to controll the speed
    speedCon.attach(pin_ESC, 1000, 2000); 
    Wire.begin();

    // Set the ESC to 0 speed so it doesn't have the motor spin right away
    speedCon.writeMicroseconds(servoZero);

    pinMode(HOVER, OUTPUT);
    pinMode(LAND, OUTPUT);

    // Wait for serial port to connect
    while (!Serial) {
        delay(1);
    }
    Serial.println("Proof Of Concept!\n\n");

    if (!vl53lox.begin()) {
        Serial.println("Failed to boot VL53L0X\n\n");
        while (1);
    } else {
        Serial.println("VL53L0X booted!\n\n");
    }

    delay(100);
}

void loop() {

    int buttonH = false; 
    int buttonL = false;

    //PID loop speed control:
    //PID constants
    const float Kp = 1.0;
    const float Ki = 0.8;
    const float Kd = 0.0;
    //PID variables
    float setpointH = 130.0; //desired hovering distance in mm
    float setpointL = 0.0; //desired landing distance in mm
    float input, output;
    float error;
    float previous_error = 0.0;
    float integral = 0.0;
    float derivative = 0.0;
    unsigned long lastTime = 0;
    unsigned long sampleTime = 100; //sample time in milliseconds

    VL53L0X_RangingMeasurementData_t distance;

    if (digitalRead(HOVER) == HIGH) {

        buttonH = true;
        Serial.println("Hovering Now!");
        delay(2000);
    }

    while (buttonH == true) {

        unsigned long now = millis();

        if (now - lastTime >= sampleTime) {

            lastTime = now;

            vl53lox.rangingTest(&distance, false);

            if (distance.RangeStatus != 4) {
                input = distance.RangeMilliMeter;
                error = setpointH - input;
                integral += error * (sampleTime / 1000.0);
                derivative = (error - previous_error) / (sampleTime / 1000.0);
                output = Kp * error + Ki * integral + Kd * derivative;

                //Constrain output to valid ESC range
                output = constrain(output, 0, 1000);
                speedCon.writeMicroseconds(servoZero + output);

                previous_error = error;

                Serial.print("Distance (mm): ");
                Serial.print(distance.RangeMilliMeter);
                Serial.print(" | Output: ");
                Serial.print(output);
                Serial.print(" | Total: ");
                Serial.println(servoZero + output);
            }
        }

        if (digitalRead(LAND) == HIGH) {

            buttonH = false;
            buttonL = true;
            derivative = 0.0;
            Serial.println("Landing Now!");
            delay(2000);

            while (buttonL == true) {

                unsigned long now = millis();

                if (now - lastTime >= sampleTime) {

                    lastTime = now;

                    vl53lox.rangingTest(&distance, false);

                    if (distance.RangeStatus != 4) {

                        setpointL = distance.RangeMilliMeter - 5;
                        input = distance.RangeMilliMeter;
                        error = setpointL - input;
                        integral += error * (sampleTime / 1000.0);
                        derivative = (error - previous_error) / (sampleTime / 1000.0);
                        output = Kp * error + Ki * integral + Kd * derivative;

                        //Constrain output to valid ESC range
                        output = constrain(output, 0, 1000);
                        speedCon.writeMicroseconds(servoZero + output);

                        previous_error = error;

                        Serial.print("Distance (mm): ");
                        Serial.print(distance.RangeMilliMeter);
                        Serial.print(" | Output: ");
                        Serial.print(output);
                        Serial.print(" | Total: ");
                        Serial.println(servoZero + output);
                    }
                }

                if (distance.RangeMilliMeter == 30) {
                    buttonL = false;
                    speedCon.writeMicroseconds(servoZero);
                }
            }   
        }
    }
}

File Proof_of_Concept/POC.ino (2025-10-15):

// Three libraries needed for POC
#include <Adafruit_VL53L0X.h>
#include <ESP32Servo.h>
#include <Wire.h>
// Making objects of the distance and ESC
Adafruit_VL53L0X vl53lox = Adafruit_VL53L0X();
Servo speedCon;
// Pins to use when wiring
const int ESC_PIN = 7;
const int WHITE = 13;
const int YELLOW = 12;
const int BLUE = 11;
const int RED = 10;
const int GREEN = 3;
const int USER = 6;

void setup() {

  Serial.begin(9600);
// Two pins being used for SDA and SCL
  Wire.setPins(8, 9);
// Setting the pin used for ESC and max/min microseconds to controll the speed
  speedCon.attach(ESC_PIN, 1000, 2000); 
  Wire.begin();

  pinMode(WHITE, OUTPUT);
  pinMode(YELLOW, OUTPUT);
  pinMode(BLUE, OUTPUT);
  pinMode(RED, OUTPUT);
  pinMode(GREEN, OUTPUT);
  pinMode(USER, OUTPUT);
// Wait for serial port to connect
  while (!Serial) {
    delay(1);
  }
  
  Serial.println("Proof Of Concept!\n\n");

  if (!vl53lox.begin()) {
    Serial.println("Failed to boot VL53L0X");
    while (1);
  }

// Set the ESC to 0 speed so it doesn't have the motor spin right away
  speedCon.writeMicroseconds(1000);

  delay(2000);
}

void loop() {

  int button = false; 

  VL53L0X_RangingMeasurementData_t distance;

  if (digitalRead(USER) == HIGH) {
    button = true;
    Serial.println("Turned on!");
    delay(2000);
  }

  while (button == true) {

      vl53lox.rangingTest(&distance, false);

      if (distance.RangeStatus != 4) {
      
      Serial.print("Distance (mm): ");
      Serial.println(distance.RangeMilliMeter);

        if (distance.RangeMilliMeter <= 200) {
          speedCon.writeMicroseconds(1300);
          digitalWrite(WHITE, HIGH);
          digitalWrite(YELLOW, LOW);
          digitalWrite(BLUE, LOW);
          digitalWrite(RED, LOW);
          digitalWrite(GREEN, LOW);
        }
        else if (distance.RangeMilliMeter > 200 && distance.RangeMilliMeter <= 400) {
          speedCon.writeMicroseconds(1400);
          digitalWrite(WHITE, HIGH);
          digitalWrite(YELLOW, HIGH);
          digitalWrite(BLUE, LOW);
          digitalWrite(RED, LOW);
          digitalWrite(GREEN, LOW);
        }
        else if (distance.RangeMilliMeter > 400 && distance.RangeMilliMeter <= 600) {
          speedCon.writeMicroseconds(1600);
          digitalWrite(WHITE, HIGH);
          digitalWrite(YELLOW, HIGH);
          digitalWrite(BLUE, HIGH);
          digitalWrite(RED, LOW);
          digitalWrite(GREEN, LOW);
        }
        else if (distance.RangeMilliMeter > 600 && distance.RangeMilliMeter <= 800) {
          speedCon.writeMicroseconds(1800);
          digitalWrite(WHITE, HIGH);
          digitalWrite(YELLOW, HIGH);
          digitalWrite(BLUE, HIGH);
          digitalWrite(RED, HIGH);
          digitalWrite(GREEN, LOW);
        }
        else if (distance.RangeMilliMeter > 800 && distance.RangeMilliMeter <= 1000) {
          speedCon.writeMicroseconds(2000);
          digitalWrite(WHITE, HIGH);
          digitalWrite(YELLOW, HIGH);
          digitalWrite(BLUE, HIGH);
          digitalWrite(RED, HIGH);
          digitalWrite(GREEN, HIGH);
        }
      }
      else {
        Serial.println("Distance can't be measured!");
          speedCon.writeMicroseconds(1000);
          digitalWrite(WHITE, LOW);
          digitalWrite(YELLOW, LOW);
          digitalWrite(BLUE, LOW);
          digitalWrite(RED, LOW);
          digitalWrite(GREEN, LOW);
      }

    if (digitalRead(USER) == HIGH) {
      button = false;
      Serial.println("Turned off!");
      speedCon.writeMicroseconds(1000);
      digitalWrite(WHITE, LOW);
      digitalWrite(YELLOW, LOW);
      digitalWrite(BLUE, LOW);
      digitalWrite(RED, LOW);
      digitalWrite(GREEN, LOW);
      delay(2000);
    }
  }
}

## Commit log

2025-11-13 Add files via upload
    PID loop code, tested it works on the actual motor and esc, proof of concept
2025-12-12 Most up-to-date version of PID code
    Most up-to-date version of PID code
    implements a PID controller for a distance-sensing application using an ESP32,
    designed to make the drone hover at a fixed distance
2025-12-17 Rename Bill of Materials - POC.pdf to Proof_of_Concept/Bill of Materials - POC.pdf
2025-12-19 Add video link of prototype in action
    Added a video link demonstrating the prototype's functionality.
